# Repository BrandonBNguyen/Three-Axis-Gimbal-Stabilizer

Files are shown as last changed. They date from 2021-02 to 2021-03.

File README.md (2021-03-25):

# Three Axis Gimbal Stabilizer

## Introduction

The goal of this project was to design and develop a gimbal system capable of stabilizing a platform based on input from an accelerometer/magnetometer sensor and to demonstrate knowledge of aerospace concepts (namely aircraft principal axes and how to calculate their orientations from accelerometer readings) and ability to apply them in a hands-on project. In aerospace, a gimbal stabilizer can be used to control the orientation of any platform or instrument where the orientation must be independent of the orientation of the aircraft, such as in a camera or targeting system.

Three-Axis Gimbal Stabilizer Showcase

## Theory

The orientation of an aircraft can be expressed as a series of rotations required to achieve that orientation starting from an initial orientation aligned with the local coordinate system, where the nose, right wing, and underside of the plane are aligned with north, east, and down, respectively, at some location on the Earth. Euler angles are the angles used to express the sequence of rotations about the principal axes of the aircraft to achieve the desired orientation from the described starting orientation. One such sequence of rotations commonly used in aerospace is yaw, pitch, and roll, where the desired orientation is described by the angle with which to yaw, then pitch, then roll the aircraft from the starting orientation aligned with the local coordinate system.

Axes body rotations as shown for a plane

To determine the roll and pitch angles to achieve the current orientation of an aircraft from an accelerometer, which measures acceleration along the body-axis angles, the following equations are used. Note that  refers to the axis pointing out the nose of the plane,  refers to the axis pointing out the right wing of the plane, and  refers to the axis pointing out the bottom of the plane.





To determine the yaw angle, the magnetometer must be used and the deflection between magnetic north and true north, 
, at the aircraft's location must be known.



Knowing the euler angles for an aircraft, a series of motors can be driven to rotate a platform in roll, pitch, and yaw, in order to keep the platform level relative to the ground regardless of the orientation of the aircraft.

## Part Selection

### Sensor Selection

The [HiLetgo MPU9250/6500](https://www.amazon.com/gp/product/B01I1J0Z7Y/ref=ppx_yo_dt_b_search_asin_title?ie=UTF8&psc=1) was selected because it contains both an accelerometer and magnetometer and would be sufficient to acquire enough information to calculate the roll, pitch, and yaw angles required to drive the motors to level the platform.

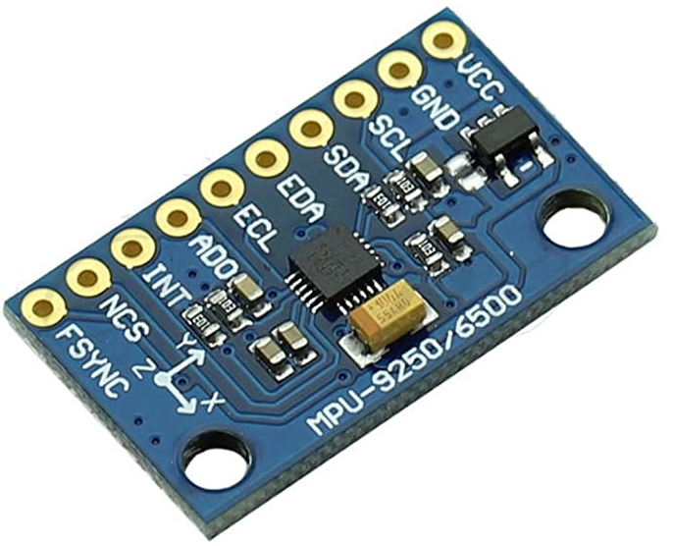
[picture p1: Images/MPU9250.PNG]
HiLetgo MPU9250/6500


### Actuator Selection

[MG90S micro servo motors](https://www.amazon.com/gp/product/B07F7VJQL5/ref=ppx_yo_dt_b_search_asin_title?ie=UTF8&psc=1) were selected to actuate the gimbals. Servo motors were selected because of the positional feedback built into them, allowing precise control over the direction of their end effectors.

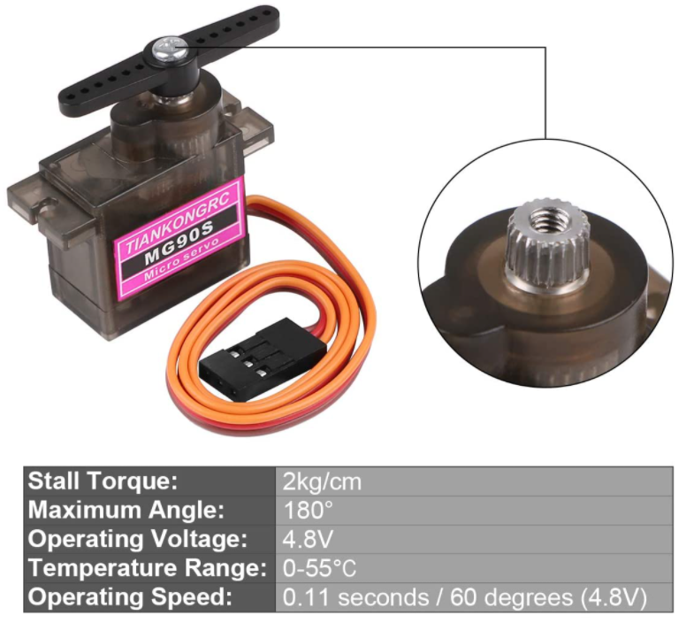
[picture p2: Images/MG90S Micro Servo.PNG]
MG90S micro servo motors


### Microcontroller Selection

An [Arduino Nano](https://www.amazon.com/gp/product/B0713XK923/ref=ppx_yo_dt_b_search_asin_title?ie=UTF8&psc=1) was used as the microcontroller for this project as it has i2c capabilities for communicating with the accelerometer and requisite PWM pins for controlling the servo motors.

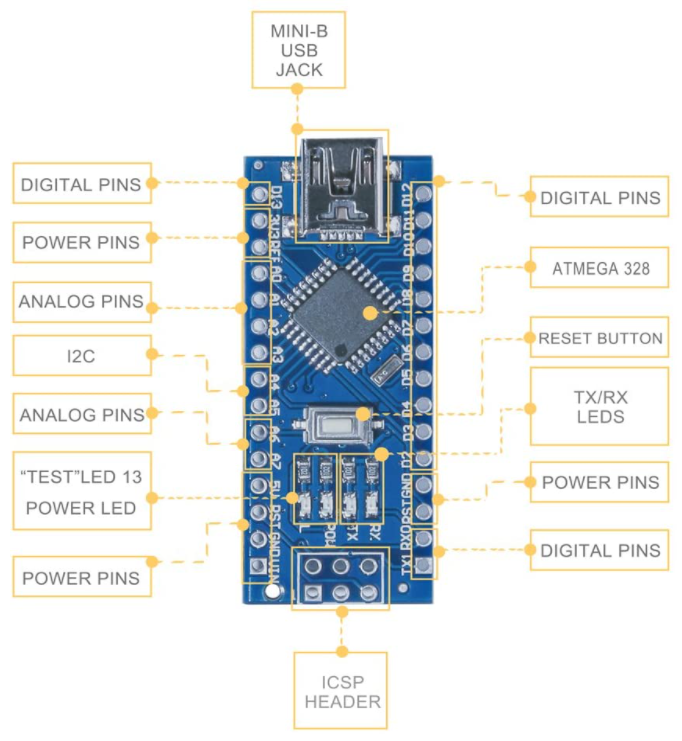
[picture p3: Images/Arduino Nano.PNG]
Arduino Nano


## CAD Model

The gimbal assembly consists of a wheel in the center capable of rotating 360° to turn to a given yaw angle. The wheel is enclosed in a ring capable of rotating 180° to turn to a given pitch angle. Finally, this ring is enclosed in another ring capable of rotating 360° to turn to a given roll angle. The yaw wheel and roll ring are driven by a gear connected to a servo with a 1:2 gear ratio in order to achieve the full 360° range of motion, since the serrvos themselves can only achieve a 180° range of motion.

The Arduino Nano and the MPU9250 accelerometer are connected to the base supporting the gimbal assembly.

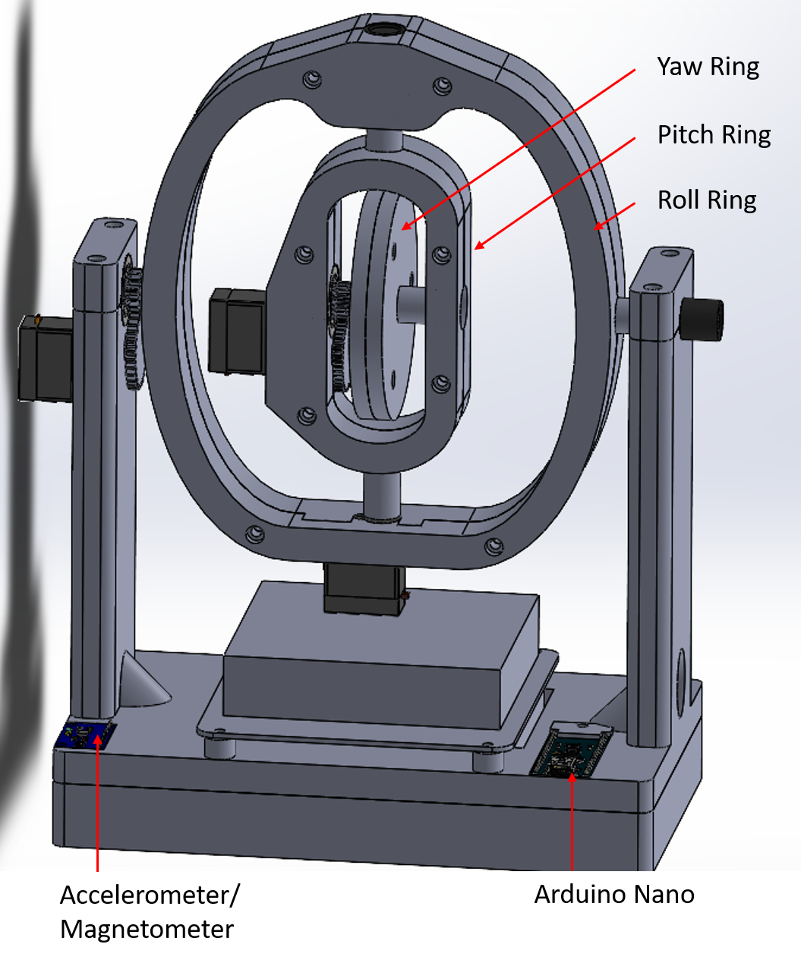
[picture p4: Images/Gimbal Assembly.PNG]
Gimbal Assembly


## Technical Challenges

### MPU9250/6500 Calibration

#### Accelerometer Calibration

Initial testing with the accelerometer yielded unexpected results as along each axis, I was getting values that were too low or too high compared to gravitational acceleration. For example, pointing the +x axis down would yield a value around 11.4 meters per second squared whereas pointing the -x axis would yield a value around -8.2 meters per second squared. Recognizing that the difference between these two values was around double gravitational acceleration, I knew that there was an accelerational offset that had to be incorporated to get the true acceleration along that axis. All axes showed the same behaviour so I had to find the offset along each axis. To find this offset, I wrote `CalibrationCode.ino`, which would average the acceleration value along all axes for 1000 trials. Each axis was aligned with the horizon before running this code to find and record the offset for each axis.

To incorporate these offsets, I wrote a class called `CalibratedMPU` which would be a subclass of `Mpu9250`, used to retrieve measurements from the accelerometer. The function, `get_readings()`, would call the parent functions `accel_x_mps2()`, `accel_y_mps2()`, and `accel_z_mps2()`, add the offsets found to the value returned by those functions, and use those as the true readings for acceleration along those particular axes. `get_readings()` then uses these values to calculate and return the pitch and roll angle.

#### Magnetometer Calibration

Magnetometer calibration involved accounting for hard iron distortion, that is distortion caused by magnetic material mounted nearby to the accelerometer, and soft iron distortion, which is caused by nearby non-magnetic materials that cause distortions to magnetic fields passing through them. Scale biases are implemented to account for both these type of distortions. Following the pseudocode provided by Mika Tuupola in [this article](https://appelsiini.net/2018/calibrate-magnetometer/), this algorithm was implemented in `MagneticCalibrationCode.ino` to find the scales and offsets. 

Finding the scales and offsets required to be applied to the raw values read from the magnetometer to get accurate readings, these corrections were implemented in the `get_readings()` function, returning corrected magnetic field readings along each axis. These, along with the calculated pitch and roll angles, are used to calculate and return the heading angle.

### Servo Calibration

Although the servo motors were marketed as having a 180° range of motion, that was not the case. In reality, the servos had about 165°~170° range of motion. Additionally, the roll and yaw rings have a 1:2 gear ratio from the output of the servo. Therefore, a scaling factor from the difference in servo command signal to the difference in actual rotation for each ring had to be found. In addition, an offset had to be found for each servo to zero the platform, which was done by leveling the base and varying the signal sent to each servo until the central platform was level. The `CalibratedServo` class was created to incorporate the scales and offsets via a linear mapping for each servo to allow them to rotate the correct amount from the zero position based on pitch, roll, and yaw angles calculated from the MPU output.

## Potential Improvements

The performance of this three-axis gimbal stabilizer can be improved by incorporating a feedback loop. This would require a second MPU to be placed on the central platform, allowing the error between the orientation of the platform and the level orientation to be measured. This error would be used to further correct the orientation, allowing better tracking.

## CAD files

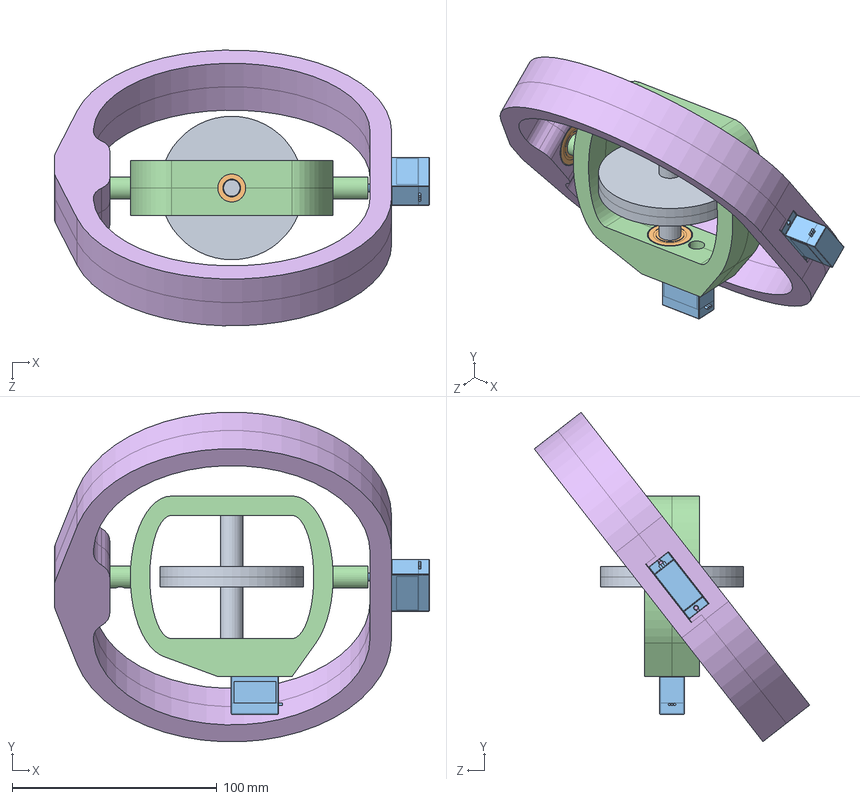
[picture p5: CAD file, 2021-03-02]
CAD/01_MAIN.SLDASM
183.0 x 160.7 x 134.4 mm
Yaw Ring^01_MAIN
608-2RS Ball Bearing x 3
Servo-MG90S x 2
Pitch Ring^01_MAIN
SlipRing
Part2^01_MAIN

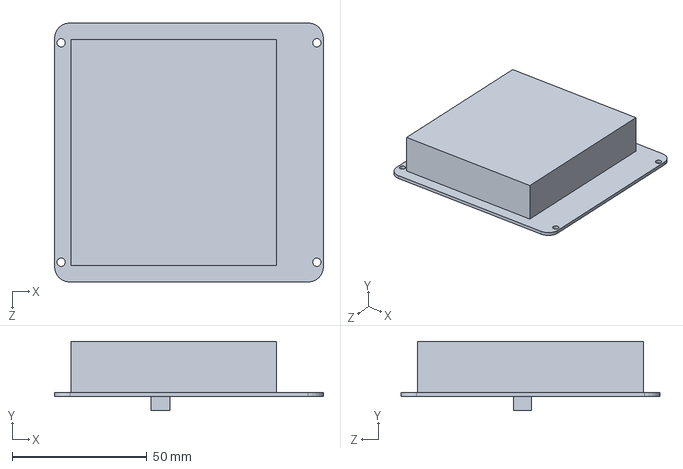
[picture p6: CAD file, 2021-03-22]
CAD/BatteryHolder.SLDPRT
99.9 x 25.7 x 96.2 mm

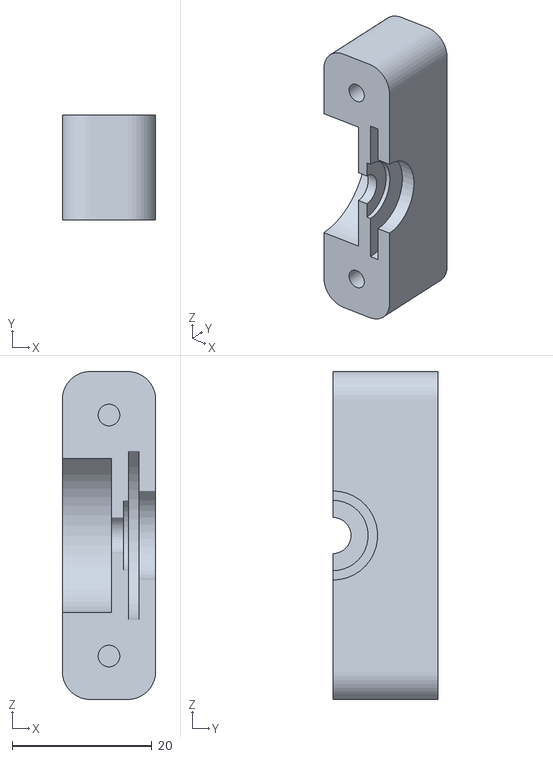
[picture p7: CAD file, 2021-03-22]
Print STL Files/Stabilizer Mount Lid (Slip Ring Side).STL
13.3 x 15.0 x 46.9

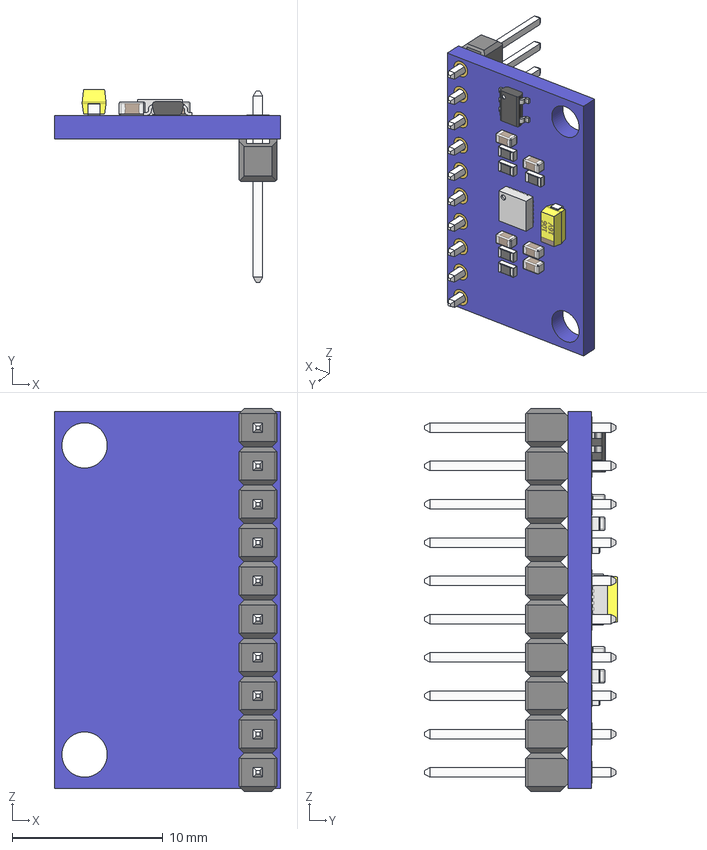
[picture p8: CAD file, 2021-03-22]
CAD/MPU-9250.stp
15.0 x 12.8 x 25.4 mm
board
hole_plating x 20
Pin Header 1x10 TH Pitch 2.54mm
MPU-9250_1
tantalum 10uF
SOT23_5
RESC-0603 x 5
CAPC-0603-T0.9-BN x 5

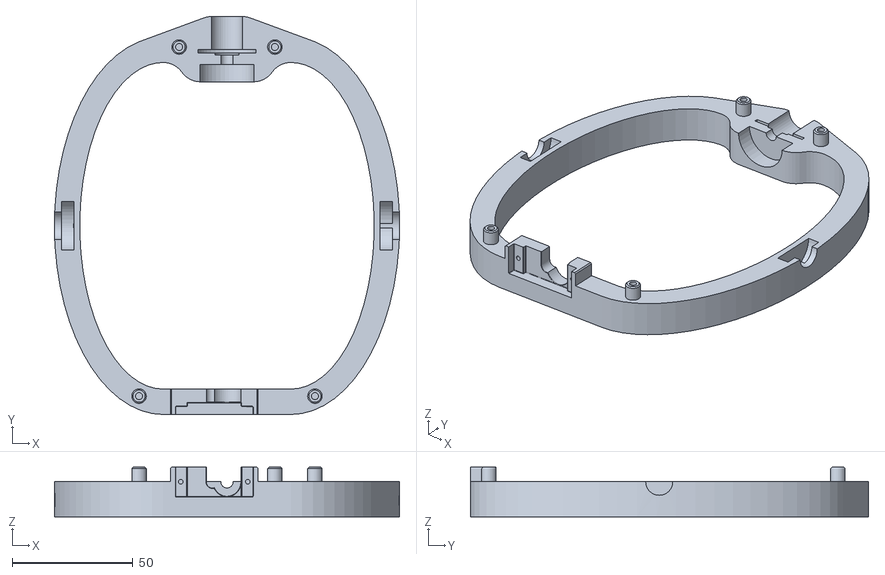
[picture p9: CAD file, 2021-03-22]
Print STL Files/Roll Ring Lower.STL
142.7 x 164.5 x 20.5

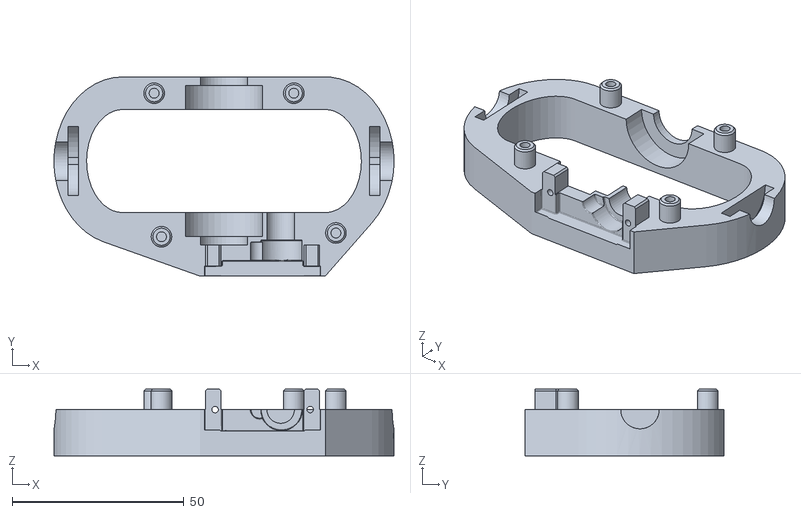
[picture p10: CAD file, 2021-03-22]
Print STL Files/Pitch Ring Lower.STL
99.0 x 58.0 x 19.5

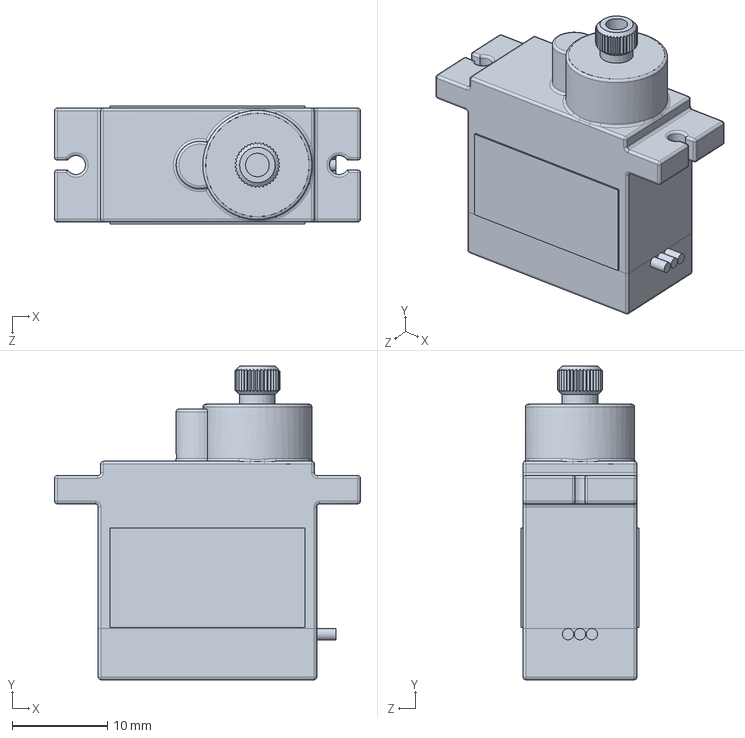
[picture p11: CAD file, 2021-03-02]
CAD/Servo-MG90S.SLDPRT
32.2 x 33.0 x 12.4 mm

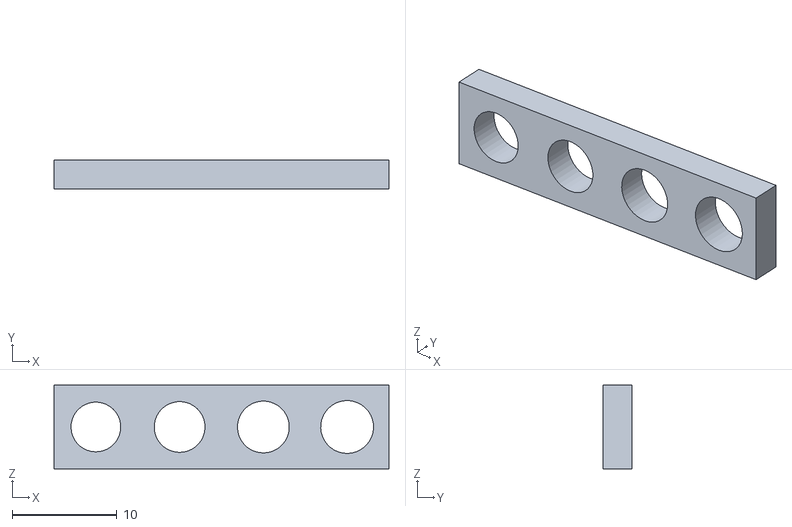
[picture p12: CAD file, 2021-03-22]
Print STL Files/Servo Motor Test Interface.STL
32.0 x 2.75 x 8.00

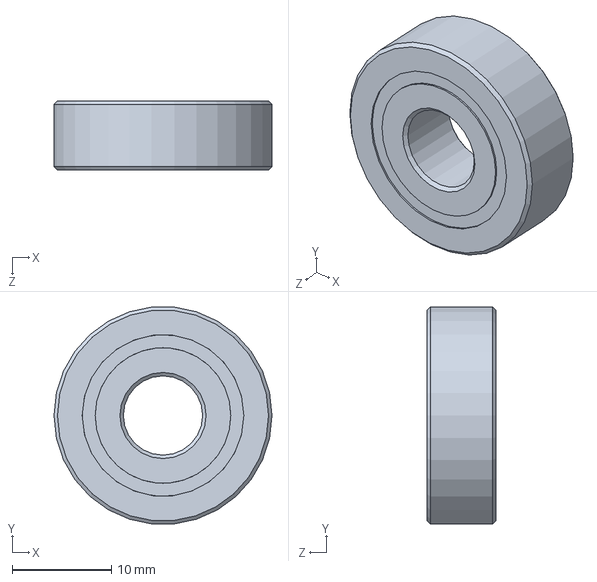
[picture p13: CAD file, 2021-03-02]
CAD/608-2RS Ball Bearing.SLDPRT
22.0 x 21.9 x 7.00 mm

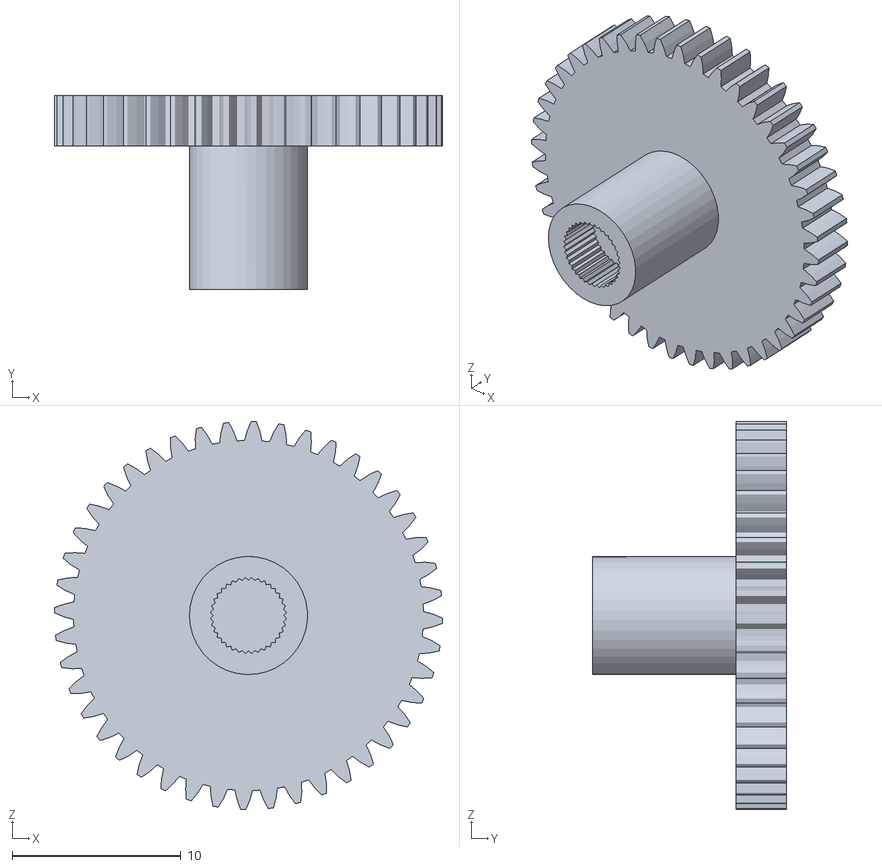
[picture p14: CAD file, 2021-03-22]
Print STL Files/Yaw Driving Gear.STL
23.0 x 11.5 x 23.0

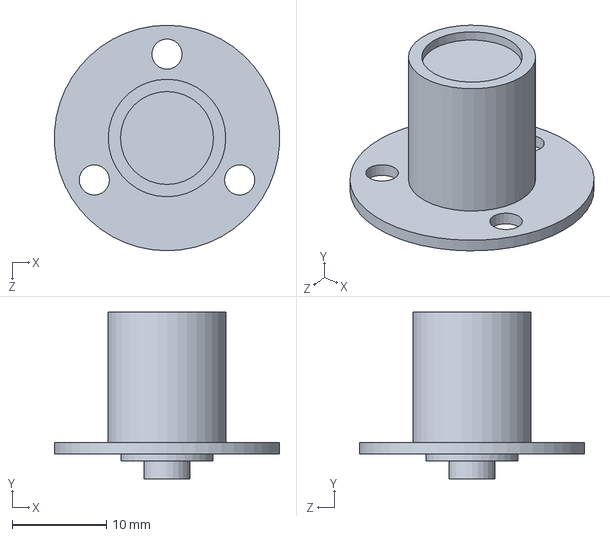
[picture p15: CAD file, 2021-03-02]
CAD/SlipRing.SLDPRT
23.8 x 17.6 x 23.9 mm

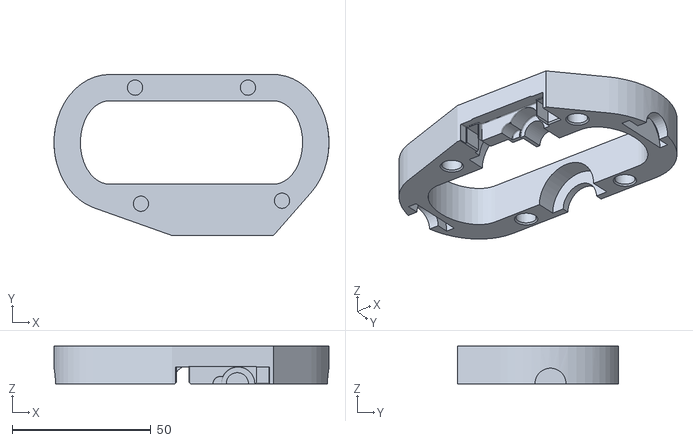
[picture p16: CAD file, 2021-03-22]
Print STL Files/Pitch Ring Upper.STL
99.0 x 58.0 x 13.5

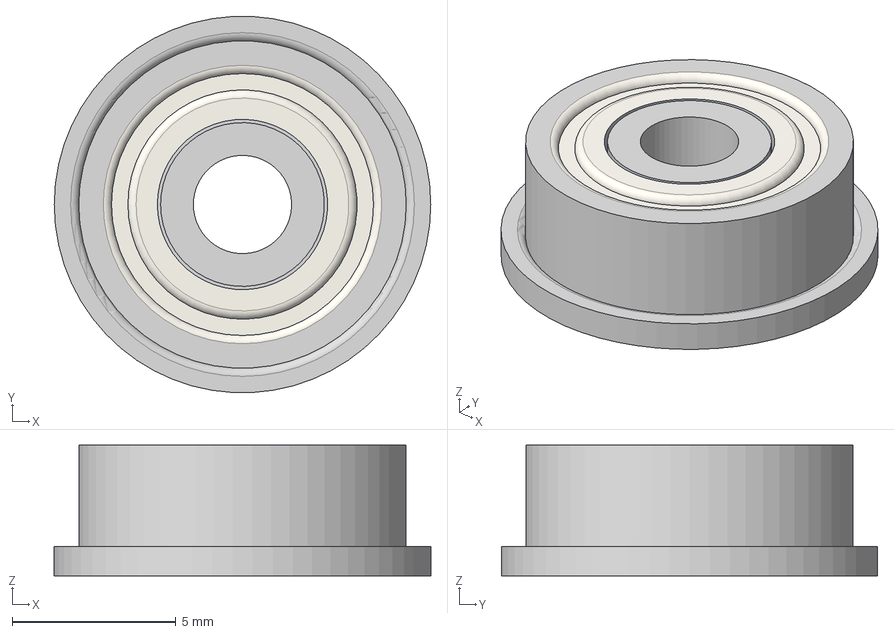
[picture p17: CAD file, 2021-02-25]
CAD/F693ZZ v1.step
11.5 x 11.5 x 4.00 mm

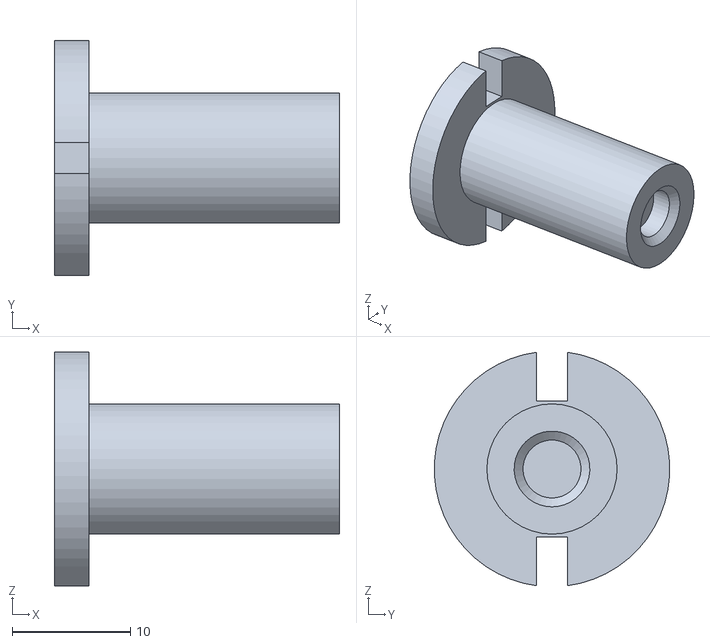
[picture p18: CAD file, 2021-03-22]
Print STL Files/Pitch Ring Servo Axle.STL
24.1 x 19.9 x 19.7

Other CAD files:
Print STL Files/Roll Ring Servo Axle.STL
Print STL Files/Yaw Ring Lower.STL
Print STL Files/Roll Ring Slip Ring Axle.STL
Print STL Files/Roll Ring Upper.STL
Print STL Files/Arduino Nano Lid.STL
Print STL Files/Mount Base.STL
Print STL Files/Pitch Ring Slip Ring Axle.STL
Print STL Files/Roll Driving Gear.STL
Print STL Files/Stabilizer Mount Lid (Motor Side).STL
Print STL Files/Stabilizer Mount.STL
Print STL Files/Yaw Ring Upper.STL

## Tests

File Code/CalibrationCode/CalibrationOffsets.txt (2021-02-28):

const auto a_x_offset = -1.62163782;
const auto a_y_offset =  1.07151603;
const auto a_z_offset =  5.31442928;

Z-Axis Up Y-Axis Left:
m_y_average: 17.59866905	m_z_average: 39.96048355

Z-Axis Down Y-Axis Right:
m_y_average: 4.18439960		m_z_average: -21.81917762

m_z_offset = -9.070652965
m_y_offset = -10.891534325

X-Axis Right:
m_x_offset: 10.59886932

X-Axis Left:
m_x_offset: -23.11783599

m_x_offset:

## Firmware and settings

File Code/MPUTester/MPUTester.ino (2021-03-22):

#include "mpu9250.h"
#include <math.h>
#include <Servo.h>

// Adjust offset based on calibration.
const auto a_x_offset = -1.62163782;
const auto a_y_offset =  1.07151603;
const auto a_z_offset =  5.31442928;
const auto m_x_offset = -3.11650466;
const auto m_y_offset = 12.11313533;
const auto m_z_offset = 16.39547157;
const auto m_x_scale = 0.91999950;
const auto m_y_scale = 0.95515546;
const auto m_z_scale = 1.15461063;

struct Reading {
    // Calibrated values to be returned by the IMU.
    const float pitch_angle;
    const float roll_angle;
    const float heading_angle;
    
    
    Reading(const float pitch_angle, const float roll_angle, const float heading_angle)
        : pitch_angle{ pitch_angle * 180 / M_PI }, 
          roll_angle{ roll_angle * 180 / M_PI }, 
          heading_angle{ heading_angle * 180 / M_PI }
    {
    
    }
};

struct CalibratedMPU : Mpu9250 {

    using Mpu9250::Mpu9250;

    Reading get_readings() {
        // Adjust x, y, and z acceleration readings based on offsets determined by calibration.
        // This is aligned such that the +x axis labeled on the accelerometer corresponds to the
        // 1-body axis, the -y axis corresponds to the 2-body axis, and the -z axis corresponds
        // to the 3-body axis.

        // Accelerometer Correction
        auto a_x =  accel_y_mps2() + a_x_offset;
        auto a_y = -accel_x_mps2() + a_y_offset;
        auto a_z = -accel_z_mps2() + a_z_offset;

        // Magnetometer Correction
        // Correct Orientation
        auto m_x =  mag_y_ut();
        auto m_y = -mag_x_ut();
        auto m_z =  mag_z_ut();
        // Correct offsets and scaling
        m_x = (m_x - m_x_offset) * m_x_scale;
        m_y = (m_y - m_y_offset) * m_y_scale;
        m_z = (m_z - m_z_offset) * m_z_scale;

        // Pitch, Roll, and Heading Angle Calculations
        auto pitch_angle = atan2(a_x, sqrt(pow(a_y, 2) + pow(a_z, 2)));
        auto roll_angle = atan2(-a_y, a_z);
        auto heading_angle = atan2(m_z * sin(roll_angle) - m_y * cos(roll_angle), 
            m_x*cos(pitch_angle) + m_y*sin(pitch_angle)*sin(roll_angle) + m_z*sin(pitch_angle)*cos(roll_angle) );
        return Reading{ pitch_angle, roll_angle, heading_angle };
    }

};

struct CalibratedServo : Servo {
    CalibratedServo(float scale, float offset) : Servo(), scale{ scale }, offset{ offset } {
      
    }

    void write(float angle) {
      Servo::write(scale * angle + offset);
    }

    private:
      float offset;
      float scale;
};

/* An Mpu9250 object with the MPU-9250 sensor on I2C bus 0 with address 0x68 */
CalibratedMPU imu{&Wire, 0x68};
CalibratedServo rollServo{(float)(89-180)/(180), 89};
CalibratedServo pitchServo{((float)89)/84 , 89};

void setup() {
    imu.Begin();
    imu.ConfigAccelRange(imu.AccelRange::ACCEL_RANGE_2G);
    rollServo.attach(3);
    pitchServo.attach(5);
}

void loop() {
    if (imu.Read()) {
        auto reading = imu.get_readings();
        rollServo.write(reading.roll_angle);
        pitchServo.write(reading.pitch_angle);
    }
}

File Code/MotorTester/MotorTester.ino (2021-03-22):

#include <Servo.h>

Servo rollServo;
Servo pitchServo;
Servo yawServo;

const int potentiometerPin{ A2 };

void setup() {
  Serial.begin(115200); // opens serial port, sets data rate to 9600 bps
  rollServo.attach(3);
  pitchServo.attach(5);
  yawServo.attach(9);
}

void loop() {
  auto outputAngle = map(analogRead(potentiometerPin), 0, 1023, 0, 180);
  Serial.println(outputAngle);
  rollServo.write(89);
  pitchServo.write(outputAngle);
  yawServo.write(0);
  delay(100);
}

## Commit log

2021-02-25 Create F693ZZ v1.step
    [F693ZZ v1.step]
2021-02-26 Added calibration code and tester code
2021-02-26 Update MPUTester.ino
    Refactored CalibratedMPU to be subclass of Mpu9250 with additional functionality of returning a Reading object with various acceleration measurements and body-axis angle measurements.
2021-02-28 Added MagneticCalibrationCode.ino
    Used to determine the offsets and scales required to produce accurate heading angle measurements from the magnetometer.
2021-02-28 Update MPUTester.ino
    Successfully displayed heading angle from calibrated accelerometer/magnetometer.
2021-03-02 Preliminary design for yaw ring
    [01_MAIN.SLDASM, 608-2RS Ball Bearing.SLDPRT, Servo-MG90S.SLDPRT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]
2021-03-02 Update 01_MAIN.SLDASM
    Added pitch ring
    [01_MAIN.SLDASM]
2021-03-02 Update 01_MAIN.SLDASM
    Added holes to mount motor in pitch ring.
    [01_MAIN.SLDASM]
2021-03-03 Update 01_MAIN.SLDASM
    Added screws for pitch and roll ring. Added gearing for yaw ring.
2021-03-22 3D print files uploaded.
    [Arduino Nano Lid.STL, BatteryHolder.SLDPRT, MPU-9250.stp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]
2021-03-24 Create Gimbal Assembly.PNG
